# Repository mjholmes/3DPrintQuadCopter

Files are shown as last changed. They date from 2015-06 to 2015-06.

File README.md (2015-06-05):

# 3D Print Quadcopter frame
### A frame designed using OpenSCAD 

This project was born from a desire to print a copy of [Dennis Baldwin's excellent mini quad frame](http://www.thingiverse.com/thing:128535) and also get to grips with [OpenSCAD](http://www.openscad.org). Using Dennis' idea I designed my own variation on his theme.
I've used the same motors as Dennis but made use of other parts I had available, all the parts he lists in the link above should work fine on this frame too.

The design uses variables to set dimensions and other key attributes of the design. Altering one setting, for example motor arm diameter, will automatically adjust corresponding elements like motor arm mounting hole etc; this for me is the real benefit of OpenSCAD.

The top plate design has mounting hole for the flight controller so it can run in either X or + configurations. Parts are attached together using standard CA model glue and clamped until they set.

Flight ready the quad weighs in at a biscuit over 200g and is very responsive in flight. I suspect it has enough power in reserve to carry a GoPro but probably not for very long. It holds it own well outdoors even in breezy conditions and can be flown indoors as well.

### Printing the parts
Within OpenSCAD you can modify the source code and comment/uncomment the particular parts you wish to print, render them and then export as STL. A pre-exported version of each part is available in the [STL subdirectory](stls/).

The frame was printed on a Makerbot Replicator 2X with most of the parts having the default "Standard" resolution settings (0.2mm layer height, 2 shells, 15% infill) with the exception of the motor mounts for which I increased the setting to 75% infill.

### Parts list
I don't know the origin of all the parts I used as some of them have been in my bits box for a while, chances are they probably came from [HobbyKing](http://www.hobbyking.com) for some project or other.

| Part | Details | Cost | Supplier |
|---|---|---|---|
| Frame | 3D printed |~40g ABS and a few hours | Me |
| Anti Vibration FC mount | 3D printed. Probably overkill if the motors/props are well balanced | 8g ABS | [ GuyMcCaldin on Thingiverse](http://www.thingiverse.com/thing:164011) |
| Motors | [Turnigy 1811 - 2900kV](http://www.hobbyking.com/hobbyking/store/uh_viewItem.asp?idProduct=36792) | £8.3/each | Hobbyking |
| Speed controllers | 10A ESCs, I had some [Robotbirds own brand models](http://robotbirds.com/catalog/product_info.php?products_id=1734). I'd recommend getting some cheaper [HK](http://www.hobbyking.com/hobbyking/store/uh_viewItem.asp?idProduct=29550) / [Turnigy](http://www.hobbyking.com/hobbyking/store/uh_viewItem.asp?idProduct=28401) units instead.  | £9/each (£4.6/unit from HK) | Hobbyking |
| Props | Some 5" CW/CCW props I had. [These props from HK](http://www.hobbyking.com/hobbyking/store/uh_viewItem.asp?idProduct=45771) *should* be fine. | ~£2.5/set  | HobbyKing? |
| Flight Controller | A KK Mini LCD. Standard 36mm form form factor | ~£11 | HobyKing |
| Rx/Tx | An FRSky FS-TH9X/FS-R8B combo which I already had | Google suggest current retail ~£70 | Any 4+ Tx/Rx should be fine | 
| Battery | A 2S 850mA LiPo. I have two Zippy Compacts | ~£4/each | Hobbyking |
| Misc M2/M3 Nylon nuts/bolts | M2 for bolting the motors and M3 for the F/C | pence | Fixings suppliers / model shops etc |
| Cabling | Rx-FC cables. I used some that I had, a better alternative is the [Super clean RC extension](http://www.hobbyking.com/hobbyking/store/uh_viewItem.asp?idProduct=67860) | £1 | Hobbyking / model shops | 
| Mounting tape | [No more nails on a roll](http://www.unibond.co.uk/en/diy-adhesives/no-more-nails/no-more-nails-on-a-roll.html). Very sticky and reduces vibration. | ~£5/roll | B&Q etc |

### Images
The frame showing all parts together, rendered and in real life
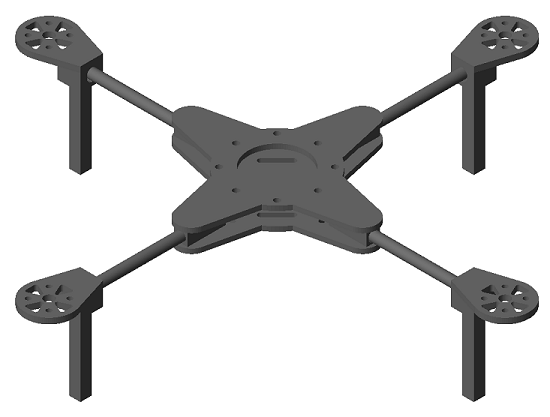
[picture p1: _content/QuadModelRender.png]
Rendered frame

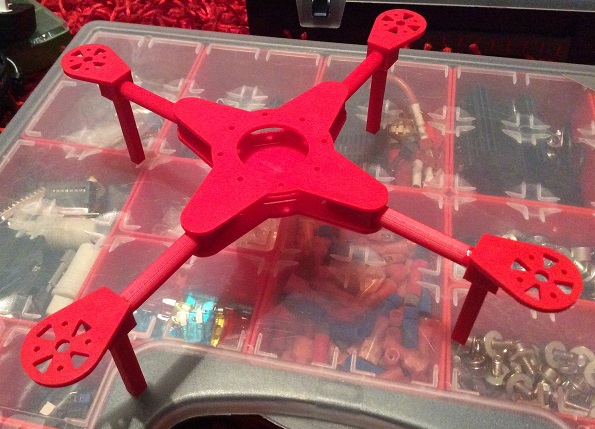
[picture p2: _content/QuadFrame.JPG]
Actual frame


The first build of the quad with all components attached. I need to improve the cable routing!
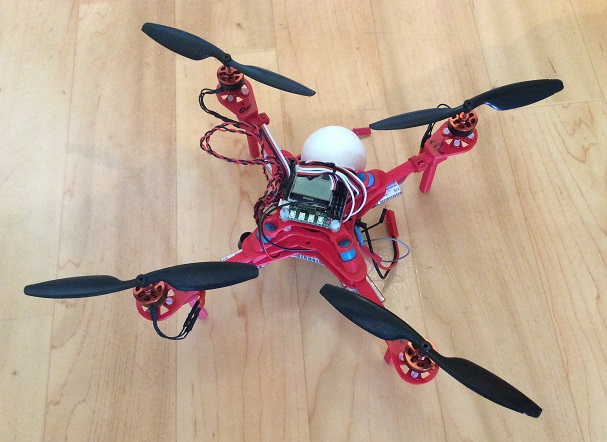
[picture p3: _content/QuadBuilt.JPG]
Fully built model


For an idea of scale, the larger quad is based on a Turnigy Talon V2 and the micro quad is a Hubsan X4.
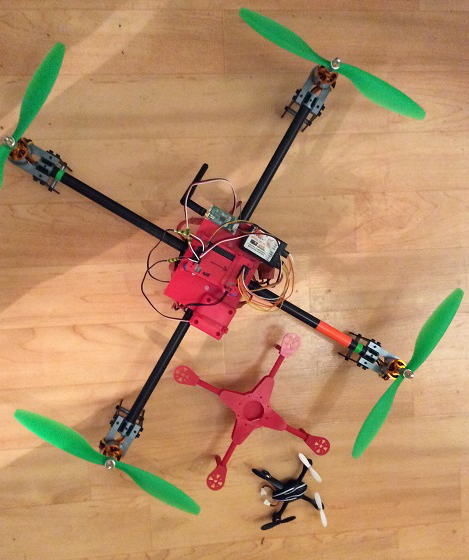
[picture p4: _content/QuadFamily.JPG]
Quadcopter family


### To do
I hope to improve on this design and as time permits i'll add more features. The wishlist currently contains:
 * Add an LED mounting point on the front for a 12mm Ultra-bright white LED to help with orientation.
 * Integrate an anti-vibration mount to the top plate rather than having a separate piece.
 * Add a mounting point for KK Mini flight controller low battery buzzer
 * Slightly increase body size (2-3mm) to give better clearance between Rx and ESC control/power cable routing slots

### License
This work is licensed under a [Creative Commons Attribution-ShareAlike 4.0 International License](http://creativecommons.org/licenses/by-sa/4.0/).

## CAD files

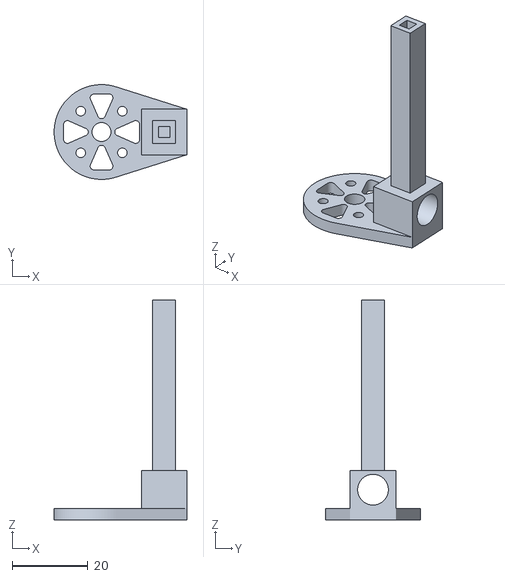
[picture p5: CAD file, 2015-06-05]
stls/QuadFrameMMount.stl
35.0 x 25.0 x 58.0

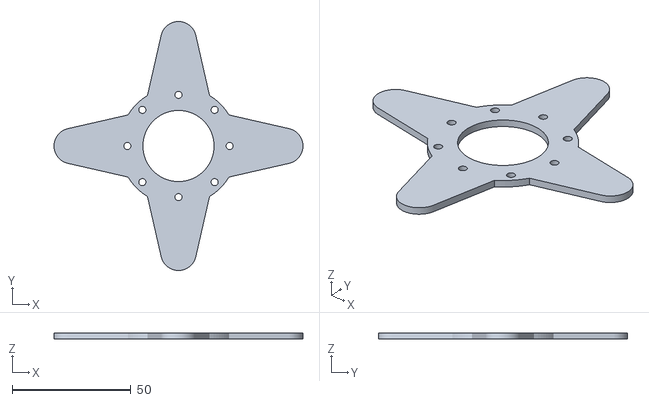
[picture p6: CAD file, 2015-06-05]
stls/QuadFrameTop.stl
105.0 x 105.0 x 2.50

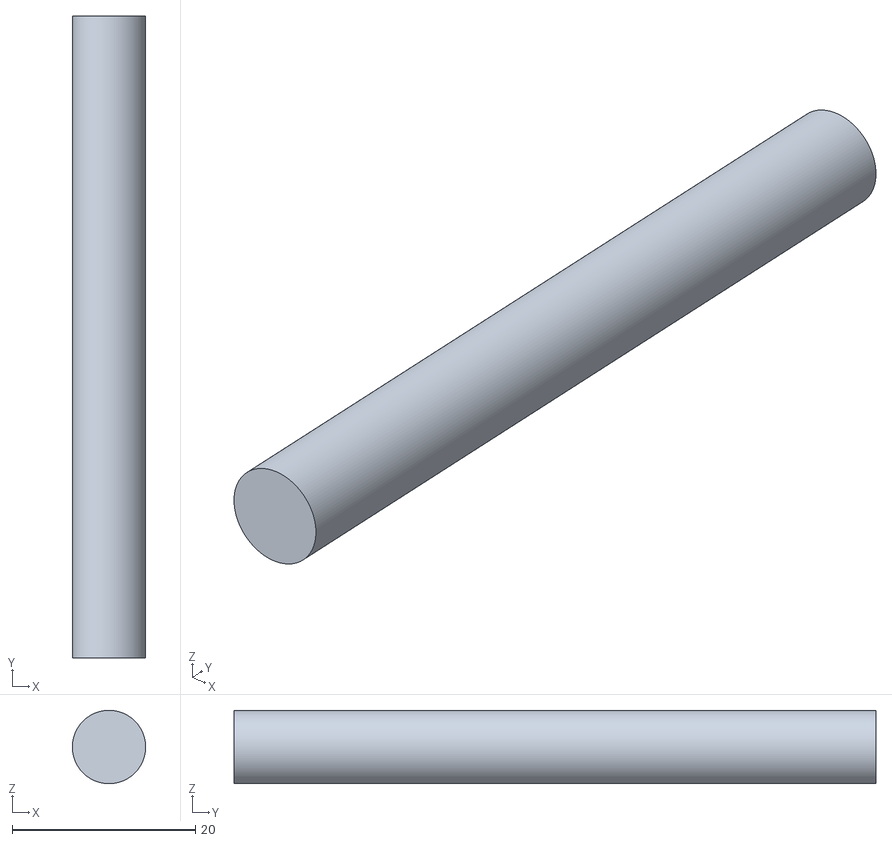
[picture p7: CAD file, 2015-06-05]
stls/QuadFrameArm.stl
8.00 x 70.0 x 8.00

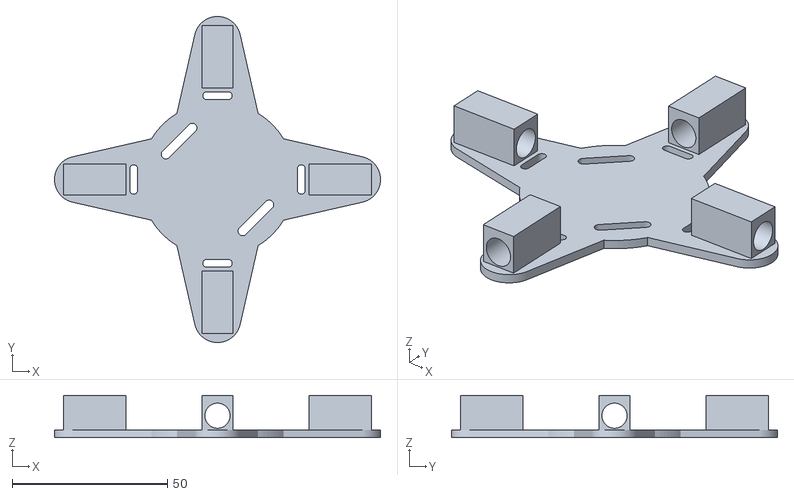
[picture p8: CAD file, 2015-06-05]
stls/QuadFrameBottom.stl
105.0 x 105.0 x 13.6

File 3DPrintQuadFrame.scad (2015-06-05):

// 3D printable mini Quadcopter frame
// Licensed under a Creative Commons Attribution License
// Matt Holmes, matt@mjholmes.org - May 2015

$fn=100;

// Some definitions
TopPieceThickness = 2.5;
BottomPieceThickness = 2.5;

MountingHoleDia = 3.0; // Dia of mounting holes for Flight contr
FCMountingCentres = 30.5; // Mounting hole centres for Flight contr

ArmDia = 8.0;
ArmLength = 70.0;
ArmMountingCubeHoleDia = ArmDia + 0.1;
ArmMountingCubeLength = 20;
ArmMountingCubeWallThickness = 1.0;
ArmMountingCubeTopRecess = 1.0;

BatteryStrapSlotWidth = 3.0;
BatteryStrapSlotLength = 12.0;
BatteryWidth = 35.0;

MMountDia = 25.0;
MMountFixingCentres = 15.5;
MMountHoleDia = 2.5;
MMountThickness = 3.0;

LGearLength = 45.0;


// Uncomment the bits you want to print or all of them
// to see a fully rendered model

//translate([0, 0, BottomPieceThickness + ArmMountingCubeVisibleHeight])
//      top_piece();

//bottom_piece();

//for ( i = [0 : 3] ) {
//    rotate( i * 360 / 4) {
//        motor_arm();
//    }
//}

//for ( i = [0 : 3] ) {
//    rotate( i * 360 / 4) {
//        translate([120,0,12])
//          rotate([180,0,180])
            motor_mount();
//    }
//}

///////////////////////////////////////////////////////
// Defs below arent usefully tweakable
TopInnerCutoutDia = 30; // Centre hole in the top piece

BodyOuterDia = 50;
BodySpokeLength = 45;
BodySpokeOuterDia = 15;
BodySpokeInternalDia = 35;


ArmMountingCubeVisibleHeight = ArmMountingCubeHoleDia + ArmMountingCubeWallThickness*2;
ArmMountingCubeHeight = ArmMountingCubeVisibleHeight + ArmMountingCubeTopRecess;
ArmMountingCubeWidth = ArmMountingCubeVisibleHeight;


// distance from edge of arm circular end to start of cube
ArmMountingCubeEdgeOffset = 1.0;

LGearMountingCubeWidth = 12.0;
LGearMountingCubeDepth = 12.0;
LGearMountingCubeHeight = 10.0;

LGearWidth = 6.0;
LGearDepth = 6.0;
LGearFudgeFactor = 2.0;
LGearWallThickness = 1.5;

///////////////////////////////////////////////////////
// Modules
module top_piece () {
difference(){
    linear_extrude(height=TopPieceThickness){
    difference(){
        union(){
            hull(){
                translate([0, BodySpokeLength, 0])
                    circle(d=BodySpokeOuterDia, center=true);
                circle(d=BodySpokeInternalDia, center=true);
                translate([0, -BodySpokeLength, 0])
                    circle(d=BodySpokeOuterDia, center=true);
            }
            hull(){
                translate([BodySpokeLength, 0, 0])
                    circle(d=BodySpokeOuterDia, center=true);
                circle(d=BodySpokeInternalDia, center=true);
                translate([-BodySpokeLength, 0, 0])
                    circle(d=BodySpokeOuterDia, center=true);
            }
            circle(d=BodyOuterDia);
        }

        // Cut out 2x4 30.5mm mounting holes for X and + config
        for ( i = [0 : 7] ) {
            rotate( i * 360 / 8) {
                translate([0,sqrt(2*pow(FCMountingCentres/2,2)),0])
                    circle(d=MountingHoleDia);
            }
        }

    
        // cut our a centre hole for wires
        circle(d=TopInnerCutoutDia);
    }
}

// Cut recess for mating arm cubes (0.1mm bigger)
// Set back from end of spoke by 1mm
    for ( i = [0 : 3] ) {
        rotate( i * 360 / 4) {
            translate([0,
                       BodySpokeLength
                         - ArmMountingCubeLength/2
                         + sqrt(pow(BodySpokeOuterDia/2,2)
                                -pow(ArmMountingCubeWidth/2,2))
                         - ArmMountingCubeEdgeOffset,
                        -ArmMountingCubeHeight/2
                          +ArmMountingCubeTopRecess])
                cube([ArmMountingCubeWidth + 0.1,
                      ArmMountingCubeLength + 0.1,
                      ArmMountingCubeHeight + 0.1], center=true);
        }
    }

}
}

module bottom_piece() {
union(){
    linear_extrude(height=BottomPieceThickness){
    difference(){
        union(){
            hull(){
                translate([0, BodySpokeLength, 0])
                    circle(d=BodySpokeOuterDia, center=true);
                circle(d=BodySpokeInternalDia, center=true);
                translate([0, -BodySpokeLength, 0])
                    circle(d=BodySpokeOuterDia, center=true);
            }
            hull(){
                translate([BodySpokeLength, 0, 0])
                    circle(d=BodySpokeOuterDia, center=true);
                circle(d=BodySpokeInternalDia, center=true);
                translate([-BodySpokeLength, 0, 0])
                    circle(d=BodySpokeOuterDia, center=true);
            }
            circle(d=BodyOuterDia);
        }
        // cut out stuff goes here
        rotate (45) hull(){ // battery strap slot 1
            translate([-BatteryStrapSlotLength/2,BatteryWidth/2,])
              circle(d=BatteryStrapSlotWidth);
            translate([BatteryStrapSlotLength/2,BatteryWidth/2,])
              circle(d=BatteryStrapSlotWidth);
        }
        rotate(45) hull(){ // battery strap slot 2
            translate([-BatteryStrapSlotLength/2,-BatteryWidth/2,])
              circle(d=BatteryStrapSlotWidth);
            translate([BatteryStrapSlotLength/2,-BatteryWidth/2,])
              circle(d=BatteryStrapSlotWidth);
        }
        
        for ( i = [0 : 3] ) { // ESC cable entry points
            rotate( i * 360 / 4) 
                translate([0,27,0])
                    hull() {
                        translate([3.5,0,0]) circle(d=2.5, center = true);
                        translate([-3.5,0,0]) circle(d=2.5, center = true);
                    }
        }   
    } // end base plate difference
}
    // Add arm mounting cubes
    for ( i = [0 : 3] ) {
        rotate( i * 360 / 4) {
            translate([0,
               BodySpokeLength
                 - ArmMountingCubeLength/2
                 + sqrt(pow(BodySpokeOuterDia/2,2)
                        -pow(ArmMountingCubeWidth/2,2))
                 - ArmMountingCubeEdgeOffset,
               ArmMountingCubeHeight/2
                 +BottomPieceThickness])
            difference(){
               cube([ArmMountingCubeWidth,
                    ArmMountingCubeLength,
                    ArmMountingCubeHeight],
                    center=true);
               translate([0,0,-ArmMountingCubeTopRecess])
                    rotate([90,0,0])
                       cylinder(d = ArmMountingCubeHoleDia, 
                                h = ArmMountingCubeLength + 2,
                                center = true);
            }
        }
    } // end arm cubes
}
}
module motor_arm() {
                   translate([0,
                              ArmLength/2 + BodySpokeLength
                                - ArmMountingCubeLength
                                + sqrt(pow(BodySpokeOuterDia/2,2)
                                    -pow(ArmMountingCubeWidth/2,2))
                                - ArmMountingCubeEdgeOffset,
                              BottomPieceThickness
                                + ArmMountingCubeVisibleHeight/2])
                    rotate([90,0,0])
                       cylinder(d = ArmDia, 
                                h = ArmLength,
                                center = true);
}
module motor_mount () {
    linear_extrude(height=MMountThickness){
    difference(){
        hull() {
            circle(d=MMountDia);
            translate([MMountDia/2 + LGearMountingCubeDepth/2
                                   - LGearFudgeFactor,
                       0,
                       0])
              square([LGearMountingCubeDepth,LGearMountingCubeWidth],
                     center=true);
        }
        for ( i = [0 : 3] ) { // motor mounting holes
            rotate( i * 360 / 4 + 45) {
                translate([0,MMountFixingCentres/2,0])
                    circle(d=MMountHoleDia);
            }
        }
        circle(d=5); // centre cutout
        for ( i = [0 : 3] ) { // triangle cutouts
            rotate( i * 360 / 4) {
                hull() {
                    translate([-2,9,0]) circle(d=2);
                    translate([2,9,0]) circle(d=2);
                    translate([0,4.5,0]) circle(d=2);
                }
            }
        }
    }
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

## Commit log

2015-05-17 Initial import
    Added version 1 of the Quad frame
    [3DPrintQuadFrame.scad]
2015-06-05 Added files from first build
    Added STL files, images and parts list from the first build of this
    frame.
    [3DPrintQuadFrame.scad, QuadFrameArm.stl, QuadFrameBottom.stl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]
2015-06-05 Fixed a couple more typos in README
2015-06-05 Added details about printing settings
